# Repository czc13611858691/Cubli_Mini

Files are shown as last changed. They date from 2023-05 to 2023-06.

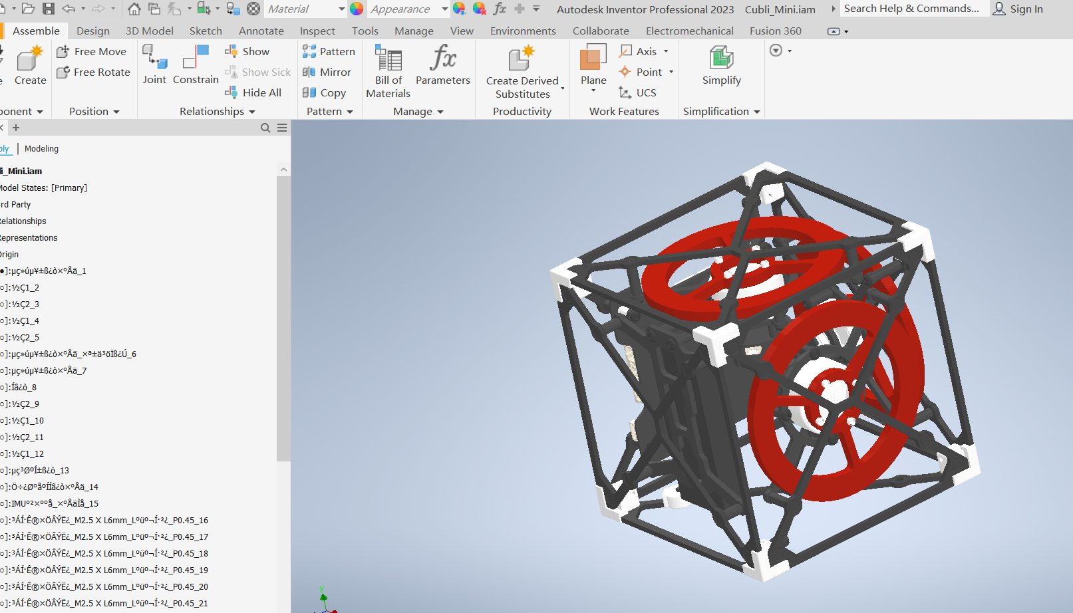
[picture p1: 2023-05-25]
Inventor工程图.png

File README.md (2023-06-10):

我的调试笔记

https://czc13611858691.github.io/Cubli_Mini/

# Cubli_Mini项目

本项目ID是来源于苏黎世联邦理工学院的Cubli，电机驱动使用的是Simple FOC。低成本、小型化、简化后作为我的首个开源项目

**项目完全开源，任何人都可以根据本Github内容自行白嫖，当然也可以顺手点个Star**

### 介绍

本项目在原版Cubli的基础上去掉主动刹车，缩小体积和一定的简化。需要手动调整到平衡点附近，才可以实现边和点平衡。Cubli_Mini是一个10x10x10CM的立方体，集电机驱动、充放电一体化。满电状态下，点平衡在无扰动下续航≥5小时。

项目成本：≤800RMB

**视频介绍：**[https://www.bilibili.com/video/BV1UR4y1c74B?spm_id_from=333.999.0.0](https://www.bilibili.com/video/BV1UR4y1c74B?spm_id_from=333.999.0.0)

YouTube：[https://youtu.be/JwiJBd6I_vY](https://youtu.be/JwiJBd6I_vY)



### 资料更新说明（2022/6/7）

- **修复**：修复PCB BOM表采购链接的部分链接错误问题，**一共有4处，已经红色标红**。已经下单的同学需要自己校验看元器件是否是正确
- **增加**：PCB BOM表采购链接里的**贴片按键增加备用链接**

### 资料更新说明（2022/5/22）

- PCB BOM表添加采购链接
- 更新<写给小白的白嫖教程.pdf><代码和工程>，图文并茂说明如何解决头文件错误问题

### 资料更新说明（2022/5/21）c23

- /6.Process/钣金件/，增加对应的step文件
- /6.Process/3D打印/，增加对应的step文件
- **安全说明**
  - **动量轮比较危险，要注意安全，手远离动量轮**
  - /2.Firmware/MCU1/control/cubli_mini.h，修改VOLTAGE_LIMIT的电压可以限制飞轮的最大输出，开始使用建议降低该参数，可以从4，5V开始

### 资料更新说明（2022/5/19)

- 最新发现动量轮有两个角忘了倒角了，理论上会影响大转速下的动平衡，因此对此进行修改。已经下单打样的同学也可以正常使用，因为电机KV值很低，我现在使用的也是漏倒角的动量轮。更新了/4.Model/Cubli_Mini.STEP文件。并且更新了/6.Process/钣金件/YC.JGJ.000002.4.*，文件版本号更新到.4
- 还有说一下结构件的采购数量和采购链接都在/6.Process/BOM/结构BOM.xls
- 物料采购的时候注意编码器模块需要3套物料

### 资料说明

- 3D模型设计源文件
- 主控模块、IMU模块、编码器模块、下载模块硬件工程
- 主控1、主控2软件工程
    - 主控模块使用两颗ESP32
- 网络调试助手
    - WIFI调参使用
- 各类文档说明
    - 对项目的一些说明，如调参，按键操作，控制原理等
- 打样文件
    - STL格式3D打印文件
    - DWG格式钣金文件
    - BOM表
        - 结构BOM表
        - PCB元器件BOM表

### 结构设计

由于我只学了一周的SW，因此有些零件会漏画一些内容，如螺丝螺纹，铜柱内螺纹啥的

外框等钣金件采用的是成本较低的玻纤板，在保证刚性的情况下降低成本。动量轮采用的是304不锈钢，可以在小体积下提供较大的转动惯量。辅以少量3D打印件组成。连接件为了美观使用的是阳极氧化铝柱，当然也可以自行使用成本更低的铜柱。整体结构件成本为350块以内，铝柱更换铜柱可以降低到290以内

**注意事项：**

- Cubli_Mini的八个角点，是由两种不同的角组成，名字为角1和角2，各4个
- 外框和角的连接处的结构不是45°对称，所以是有安装方向的，详情看DoC/结构和安装说明

### 电路模块

**主控模块：**

- 主控模块集成了3个电机驱动电路，电池充放电路，降压稳压电路，CAN通讯电路
- 由于单颗ESP32只有6路电机PWM，因此使用了两颗ESP32模块，使用了CAN作为MCU间的通讯方式，由于两颗ESP32都是集成在同一个主板上，因此为了节省IC成本，可以把CAN修改为IIC，UART，SPI等各类短路径通讯方式，但是需要修改主控软硬件，有想法的同学可以自行修改
- 电机驱动电路参考Simple FOC开源电路，Simple FOC链接：[https://github.com/simplefoc](https://github.com/simplefoc)。电池充放电参考：[https://oshwhub.com/qqj1228/zi-ping-heng-di-lai-luo-san-jiao_10-10-ban-ben](https://oshwhub.com/muyan2020/zi-ping-heng-di-lai-luo-san-jiao_10-10-ban-ben_copy)

**IMU模块：**

- 使用最为常见的MPU6050
- 为了防止应力，对IMU所在区域挖槽，减少安装应力。但使用了3颗螺丝硬连接，并不能避免应力问题，改进方案为使用软垫片并只拧紧一个螺丝进一步减少应力
- 由于IMU安装要求比较高，因此在贴片时，尽量保证MPU6050与PCB平行，且位于焊盘正中央

**编码器模块：**

- 采用的是成本较低的AS5600，在低速情况下便宜好用

**自动下载模块：**

- 为了尽量减少主控的面积，因此单独把自动下载电路摘出来，参考官方自动下载电路

**注意事项：**

- 正常情况下，自动下载模块焊接排针，主控不焊接任何排针/排母

### 固件说明

Cubli_Mini的核心内容为Simple FOC电机驱动库以及点平衡控制算法，运行在MCU1中。MCU2只是使用了Simple FOC库对电机2和电机3的控制，利用CAN反馈和接收控制命令。

**MCU1固件说明：**

- bsp：基于arduino库封装了一下LED，KEY，ADC，非易失储存等内容
- comm：公用类，目前只封装了一个时间类，获取时间差，非延时等待等简单内容
- control：核心库，内容为平衡算法和调参接口，调参参考Simple FOC格式。为方便使用，使用的是字符串，不使用传统的16进制协议
- main：main文件，驱动的初始化和FreeRTOS任务创建
    - ESP32官方把WIFI，蓝牙类运行在Core0。因此在创建任务中，把WIFI任务创建在Core0中，其他则创建在Core1。只有运行于不同核心任务的数据交互我才加了互斥锁。

**注意事项：**

- 目前WIFI SSID和PSW，TCP Server IP Port全部是写死在固件里面，因此要想使用WIFI调参需要修改这些内容，详情请看Doc/使用和调参说明

### 打样说明

考虑到很多同学可能是第一次进行结构打样，因此提供了打样文件

**3D打印：**

- 文件位于：/6.Process/**3D打印**，该文件为STL格式，打样数量请查看同目录下的<**3D打印加工说明**>，可以在未来工厂或者嘉立创打样，首选光固化
- 文件名称使用的是料号，料号方便管理，尾号没有.X都代表为第一版

**钣金件打样：**

- 文件位于：/6.Process/**钣金件**，**每个物料的都有对应的PDF和DWG文件，PDF文件方便查看，DWG文件用于激光切割/板材加工**。打样数量请查看同目录下的<**钣金加工说明**>，可以找淘宝给图纸直接加工。由于加工精度要求不高，个人用途下，公差全看加工厂的心情
- 也可以直接找到对应的step文件给淘宝加工

**PCB打样：**

- 从硬件工程拿着PCB文件出门左转嘉立创白嫖

**BOM表：**

- 文件位于：/6.Process/**BOM**
- 结构BOM表，里面列有需要购买的**结构物料和链接**
- PCB BOM表，里面列有需要购买的元器件物料，也可以自行找到AD工程导出
- **注意事项：**
    - PCB BOM表是从AD源文件导出，工程会有重复用料，需要注意
    - **注意编码器需要3块，需要采购3套物料**
    - DRV8313、ESP32、AS5600、IMU可以去淘宝购买，其他右转立创商城BOM表下单。
    - **注意贴片型铝电解电容的封装，主控板有限高区域，限高高度为8mm**
    - 如文件有遗漏的地方望提醒

**写给小白的白嫖教程：**

- 文件位于：/Doc/写给小白的白嫖教程.pdf，手把手教你如何完成本项目的白嫖

### 控制算法

Cubli_Mini使用的是LQR来进行控制，也可以使用串级PID来进行控制。代码位于/需要修改/MCU1/control/cubli_mini

**边平衡**：

- 可以参考一阶倒立摆进行建模和求解参数。由于建立模型的参数比较难准确的获得，我求解得到的参数和最佳参数有些许出入。因此本项目大多数使用玄学调参工程师来整定参数

**点平衡：**

- 在边平衡的基础上添加对X，Z轴的控制。采用与边平衡一样的控制方法，详情看Doc/控制原理说明。

**研究型：**

- 请查看原版Cubli的论文

### 调参

**调节方法：**

- 可以使用UART和WIFI进行调参，WIFI需要连接到路由器，Cubli_Mini为TCP客户端

**调节命令：**

- 详情命令请查看Doc/调参命令说明

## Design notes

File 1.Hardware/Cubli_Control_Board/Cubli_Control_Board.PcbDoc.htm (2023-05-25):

Reporting Options

# File in Previous Format

Date | : | 2023/5/26
Time | : | 7:39:50
Filename | : | C:\Projects\Cubli_Mini\1.Hardware\Cubli_Control_Board\Cubli_Control_Board.PcbDoc

Version | Warning

This file was generated by an earlier version of the software

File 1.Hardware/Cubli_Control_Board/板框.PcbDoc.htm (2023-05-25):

Reporting Options

# File in Previous Format

Date | : | 2023/5/26
Time | : | 7:40:09
Filename | : | C:\Projects\Cubli_Mini\1.Hardware\Cubli_Control_Board\겼움.PcbDoc

Version | Warning

This file was generated by an earlier version of the software

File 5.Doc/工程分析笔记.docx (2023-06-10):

工程分析笔记

# 1. 工程MCU引脚

platformio.ini文件中提供了开发板的信息

根据github文档指引可以找到文档如下

ESP32-PICO-KIT V4/V4.1 入门指南 (https://docs.espressif.com/projects/esp-idf/zh_CN/latest/esp32/hw-reference/esp32/get-started-pico-kit.html)

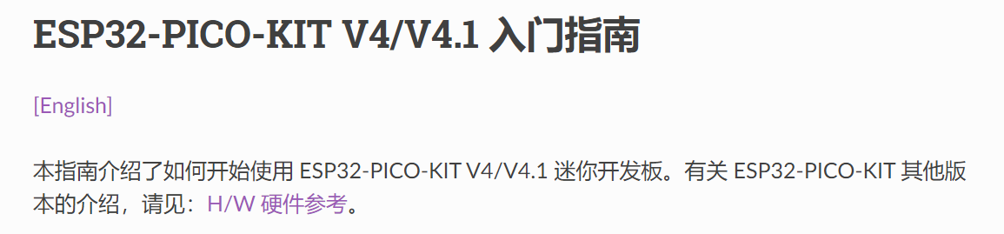
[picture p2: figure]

引脚定义图如下

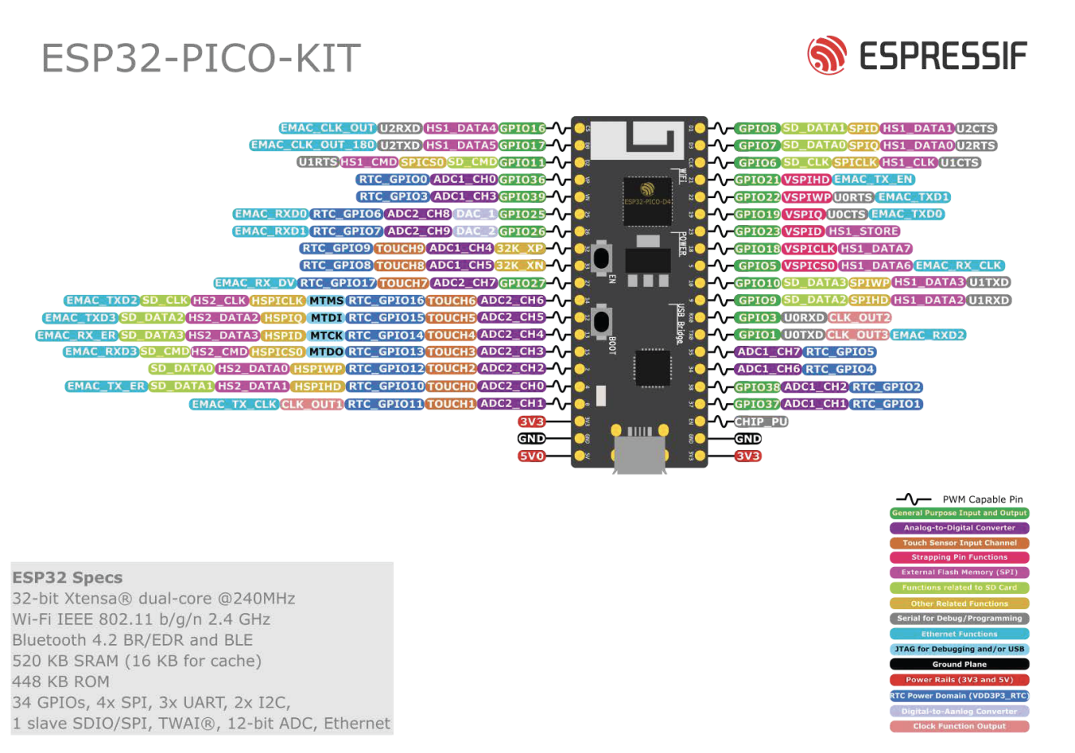
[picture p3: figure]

ESP32已经支持CAN总线,其引脚命名为TWAI，使用ESP32玩转CAN总线（1） (https://blog.csdn.net/zengqz123/article/details/111165302)。

可以支持调试?

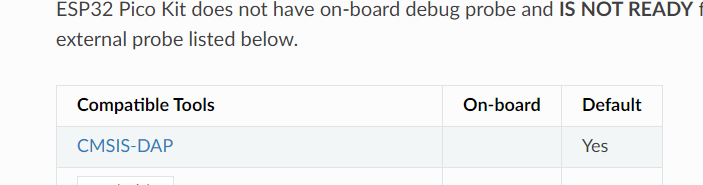
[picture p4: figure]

引脚定义如何联系到板子上的引脚标号?

#define MOTOR_1_PWM1_PIN (int)25

#define MOTOR_1_PWM2_PIN (int)26

#define MOTOR_1_PWM3_PIN (int)27

#define MOTOR_1_EN_PIN (int)33

#define MOTOR_1_SENSOR_I2C_SDA_PIN (int)4

#define MOTOR_1_SENSOR_I2C_SCL_PIN (int)14

#define CAN_TXD_PIN (int)15

#define CAN_RXD_PIN (int)13

#define IMU_SCL_PIN (int)18

#define IMU_SDA_PIN (int)5

#define IMU_INTERRUPT_PIN (int)23

#define BULE_LED_PIN (int)10

#define GREEN_LED_PIN (int)9

#define MOTOR_GREEN_LED_PIN (int)21

#define KEY_1_PIN (int)22

#define KEY_2_PIN (int)19

#define BAT_VOLTAGE_PIN (int)36

参考如下管脚说明 (https://docs.espressif.com/projects/esp-idf/zh_CN/latest/esp32/hw-reference/esp32/get-started-pico-kit.html)

对应其中的GPIOx,对应关系示例如下:

BAT_VOLTAGE_PIN 36 GPIO36

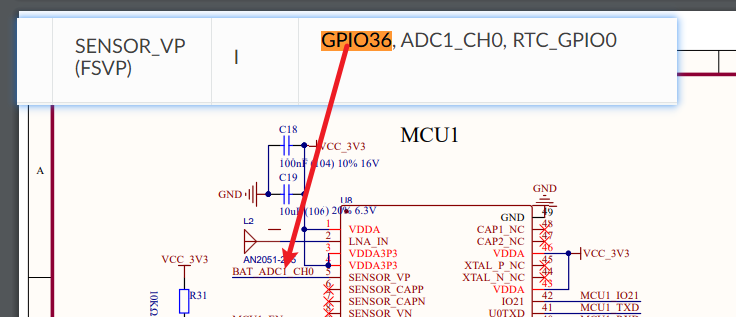
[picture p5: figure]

# 2. 关键控制算法学习

关键控制算法位于cubli_mini.cpp文件中，void CubliMiniControl::Control()是不同控制模式的切换入口。ePOINT_BALANCE代表单点平衡模式，eUNILATERAL_BALANCE 代表单边平衡模式。

float x_axis_speed = Lqr(p_balance_.sensor.x, p_balance_.param.x);

LQR是什么意思?

推测是一种类似PID的控制算法。

LQR算法最后得出电机需要力矩。

simple foc使用的是电压力矩控制模式。

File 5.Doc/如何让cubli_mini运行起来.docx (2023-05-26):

# 1. 材料购买

## 1.1. 电子

### 1.1.1. PCB打样

### 1.1.2. 物料购买

## 1.2. 结构

### 1.2.1. 3D打印件

### 1.2.2. 钣金件

### 1.2.3. 螺丝

## 1.3. 工具

# 2. 焊接

# 3. 组装

# 4. 代码编译与调参

# 5. 原理学习

# 6. 变更

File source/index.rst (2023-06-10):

.. cubli_mini documentation master file, created by
   sphinx-quickstart on Sat Jun 10 11:38:40 2023.
   You can adapt this file completely to your liking, but it should at least
   contain the root `toctree` directive.

cubli_mini
======================================

.. toctree::
   :maxdepth: 2
   :caption: Contents:

   note/论文pdf.md

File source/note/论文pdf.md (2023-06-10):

# 论文pdf

[论文1-Cubli_ECC2013.pdf](../file/Cubli_ECC2013.pdf)

[论文2-Cubli_IROS2012.pdf](../file/Cubli_IROS2012.pdf)

[论文3-cubliCDC13.pdf](../file/cubliCDC13.pdf)

[论文4-RevisedManuscript.pdf](../file/RevisedManuscript.pdf)

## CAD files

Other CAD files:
4.Model/InventorPrj/2715µç»ú.iam
4.Model/InventorPrj/2715µç»ú_1.iam
4.Model/InventorPrj/2715µç»ú_2.iam
4.Model/InventorPrj/2715µç»ú»ù×ù.ipt
4.Model/InventorPrj/2715µç»úÍ·.ipt
4.Model/InventorPrj/402764µç³Ø-3S.ipt
4.Model/InventorPrj/=_[0_1_1_10]^SW-SMD_LSSAM12-V-T-R.STEP.ipt
4.Model/InventorPrj/=_[0_1_1_8]^SW-SMD_LSSAM12-V-T-R.STEP.ipt
4.Model/InventorPrj/COMPOUND^CONN-SMD_HC-1.0-7PWT.STEP.ipt
4.Model/InventorPrj/CONN-SMD_3P-P1.0-HC-1.0-3PWT.STEP.iam
4.Model/InventorPrj/CONN-SMD_5P-P1.00_HCTL_HC-1.0-5PLT.ipt
4.Model/InventorPrj/CONN-SMD_5P-P1.00_HCTL_HC-1.0-5PWT.iam
4.Model/InventorPrj/CONN-SMD_HC-1.0-7PWT.STEP.iam
4.Model/InventorPrj/Cubli_Mini.iam
4.Model/InventorPrj/IMU_PCB.iam
4.Model/InventorPrj/IMU°²×°°å.ipt
4.Model/InventorPrj/IMU°²×°°å_×°ÅäÌå.iam
4.Model/InventorPrj/LOGO__0.5^PH2.0_SMD-W-2P_PH__ģʽ(2)_ģʽ.ipt
4.Model/InventorPrj/M2.5D4Í¨¿×ÂÁÖù_2x12mm.ipt
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

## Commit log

2023-05-25 增加论文文档
2023-05-25 增加html bom
2023-05-25 原版step文件导入到inventor设计软件
    [2715µç»ú.iam, 2715µç»ú_1.iam, 2715µç»ú_2.iam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]
2023-05-25 根据我的电脑上的spi.h和wire.h的位置修改库的路径
2023-05-25 导出cubli_control_board原理图pdf文件
2023-05-26 增加文档，计划分析每个引脚的标号
2023-05-26 增加文档
2023-06-10 工程分析笔记文件更新
2023-06-10 上传文件以后文档采用sphinx+github pages的方式
2023-06-10 文档中增加论文描述
2023-06-10 修改文档资源无法打开的错误
2023-06-10 更新文档构建的bat程序
2023-06-10 修改文档
